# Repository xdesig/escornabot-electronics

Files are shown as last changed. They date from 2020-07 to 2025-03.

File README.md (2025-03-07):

# escornabot
Educational robot
scornabot is an open source/hardware project that aims to bring robotics and programming to children.

The basic Escornabot can be programmed with the robot's buttons to execute sequence of movements. From this, imagination is the only one limit to the possibilities.

- Hey! That you are describing looks very much like a Bee-Bot!

- Yes, but much better for several reasons. Among them, I will highlight a few:

It is made by you. And your pupils, children, young cousins... Everyone can help by participating in the process from the beginning. The pleasure of building your own escornabot converts the experience in something great, specially when children are involved in it.

It is a open hardware (OSHW) and free software (FOSS) so you can adapt its characteristics to your needs: to put sensors, LEDs, change the aperture angle of rotation, the distance it moves at each step... whatever that comes to mind.

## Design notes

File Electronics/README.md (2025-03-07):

## Catalog
- [Escorna CPU][CPU01] is 50x50mm to 50x100mm board to use with Arduino Nano. It integrates keypad on board on 2x

- [Escorna_CPU_2_4][CPU240] It is a pcb that integrates an ATmega328P, a step-up (to use 1.2V batteries) and the rest of the electronics needed to build an Escornabot.

- [Arduino Shield][ARD01] is an Arduino Uno compatible
  shield ready to use with the Escornabot's motors and also integrates a keypad.

- [Cervus][CER01] is a board based on powerful ATmega32u4
  microcontroler and compatible with Arduino shields.
- [E_Keypad][KEY01] Is a 50x50mm board with 6  and 5 buttons and
  connects to any Escornabot.

- [E_KEY_BT][E_KEY_BT] Escornabot keyboard with MakeyMakey type sensors on the E_KEY_BT board.
   Any object that is minimally conductive can be used. Adjusting the value
   threshold: higher for less sensitivity, nothing needs to be changed in the
   robot firmware.

- [E_KEY_FICHA][E_KEY_FICHA] It allows the programming of Escornabot using printed or cut-out cards (cardboard ..) communicating the commands via Bluetooth.
  using @arduino Nano, easy to print, manageable and expandable to 15 "Tabs" thanks to the firmware of @caligari_pub

- [escoRnaFID][RnaFID]PCB for the project for children with visual impairment or blindness,
  developed by Angel Villanueva [@avilmaru][@avil] to control an Escornabot with RFID cards

## License

Every content in this repo, otherwise specified under subdirectories, is
licensed under [Creative Commons BY-SA][LICENSEcc] or [CERN Open Hardware Licence -W- V2][OHL-W-V2].
(by [XDeSIG][XDE01])

## To buy boards

Developer don't produce boards to sell. Under [_provider_][provider]
directory there are instructions to order yourself.

Are you a board provider? Please, send us your buyer's guide! :-)

[CPU01]: EscornaCPU
[CPU240]: https://github.com/xdesig/escornabot-electronics/tree/master/Electronics/EscornaCPU/2.x/2.40
[ARD01]: ArduinoShield
[CER01]: Cervus
[KEY01]: E_KEYPAD
[RnaFID]: escoRnaFID
[E_KEY_BT]: E_KEY_BT
[@avil]: https://twitter.com/avilmaru
[XDE01]: https://twitter.com/xdesig
[provider]: https://www.pcbway.com/project/member/?bmbno=6FE4DE76-9D11-4C
[LICENSEcc]: https://creativecommons.org/licenses/by-sa/3.0/es
[OHL-W-V2]: https://ohwr.org/project/cernohl/wikis/Documents/CERN-OHL-version-2

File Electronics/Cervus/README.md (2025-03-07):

# Cervus 2.001

## Catalog

- [Cervus][KEY01] (by [Xdesig][XDE01]) is a 50x50mm board, it controls any Escornabot, and is an atmega development PCB (Arduino Leonardo compatible)

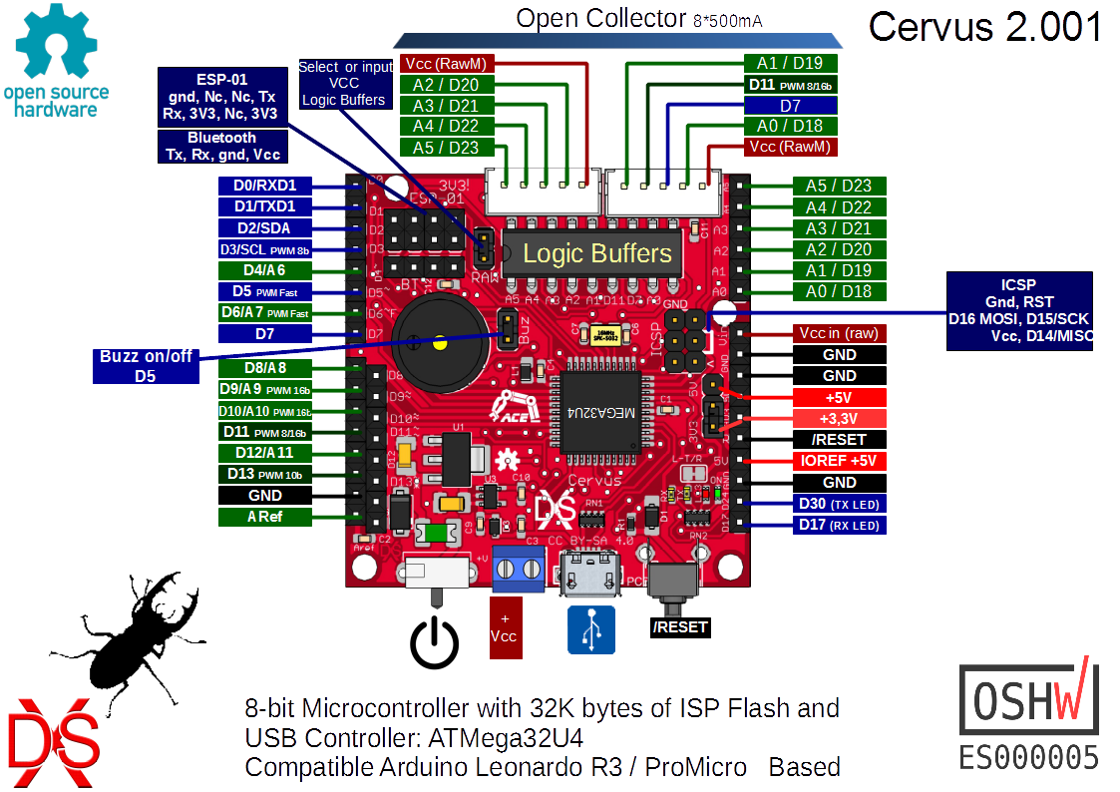
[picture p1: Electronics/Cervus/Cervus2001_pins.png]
Top view


## License

Every content in this repo, otherwise specified under subdirectories, is
licensed under [Creative Commons BY-SA](LICENSE).

## To buy boards

Developers don't produce boards to sell. Under [PCBWAY]

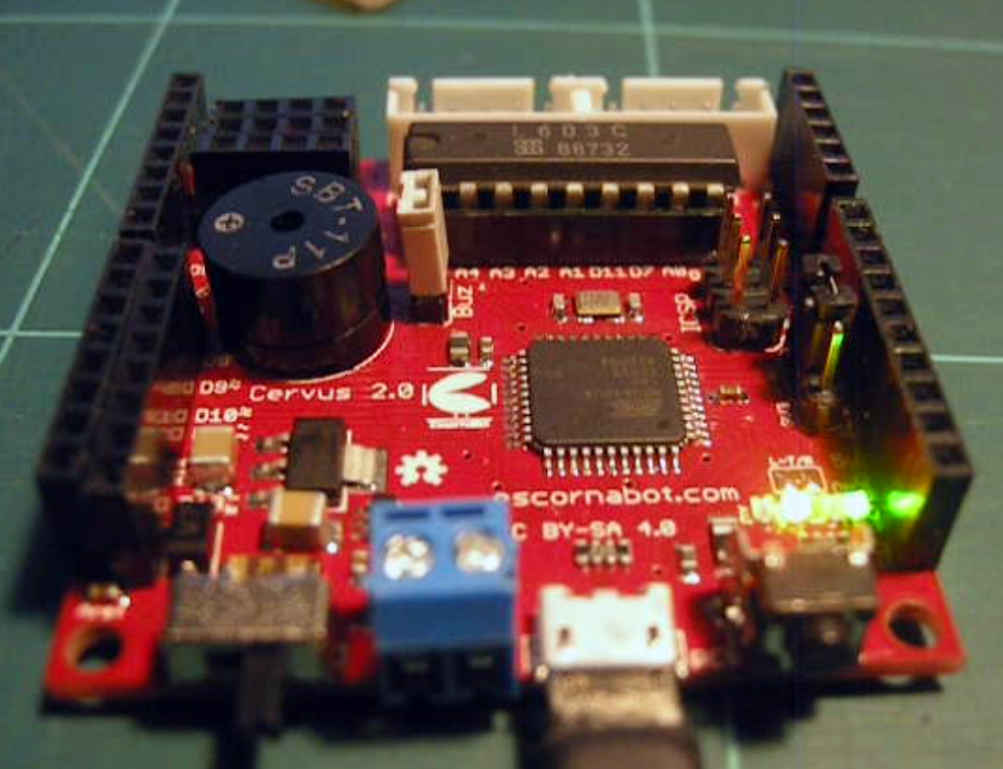
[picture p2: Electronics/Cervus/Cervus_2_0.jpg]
Bottom view


[KEY01]: Keypad
[PCBWAY]: https://www.pcbway.com/project/shareproject/Cervus_Arduino_Leonardo_Coompatible.html
[XDE01]: https://twitter.com/xdesig

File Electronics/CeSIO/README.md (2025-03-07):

# CeSIO Cervus Shield I/O  V 000

A pcb with all the I / O of Cervus (compatible with Arduino PCBs), available in connectors accompanied by + V and Gnd, whereby groups we can choose how we feed it: a + 5V, A + 3.3V or external V, giving the possibility to connect elements such as sensors, servos and other devices, has connector for ESP01 and Bluetooth.

It allows to use the DD05CVSA module to control a Li-ion battery.

Buy PCB in [PCBWAY]

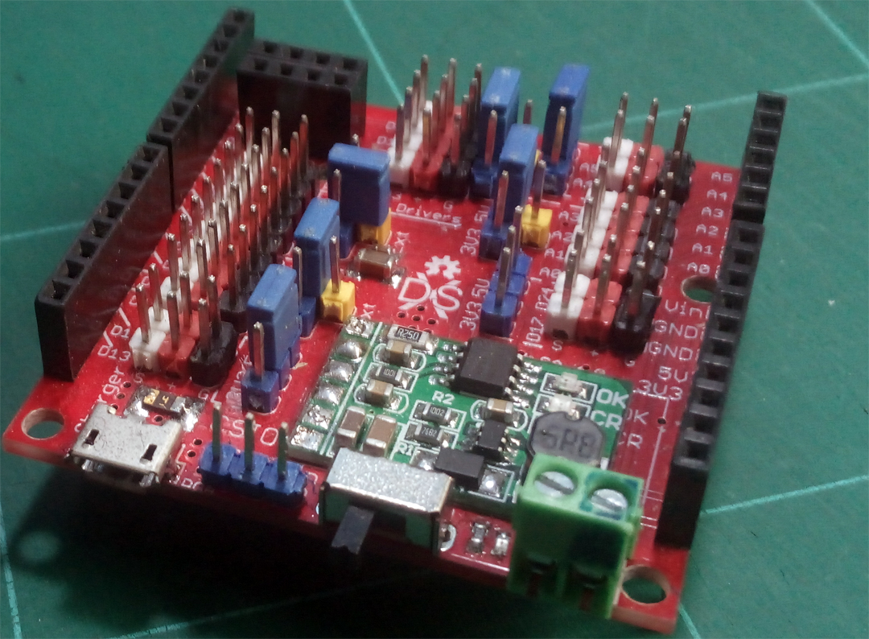
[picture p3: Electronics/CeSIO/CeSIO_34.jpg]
Top view

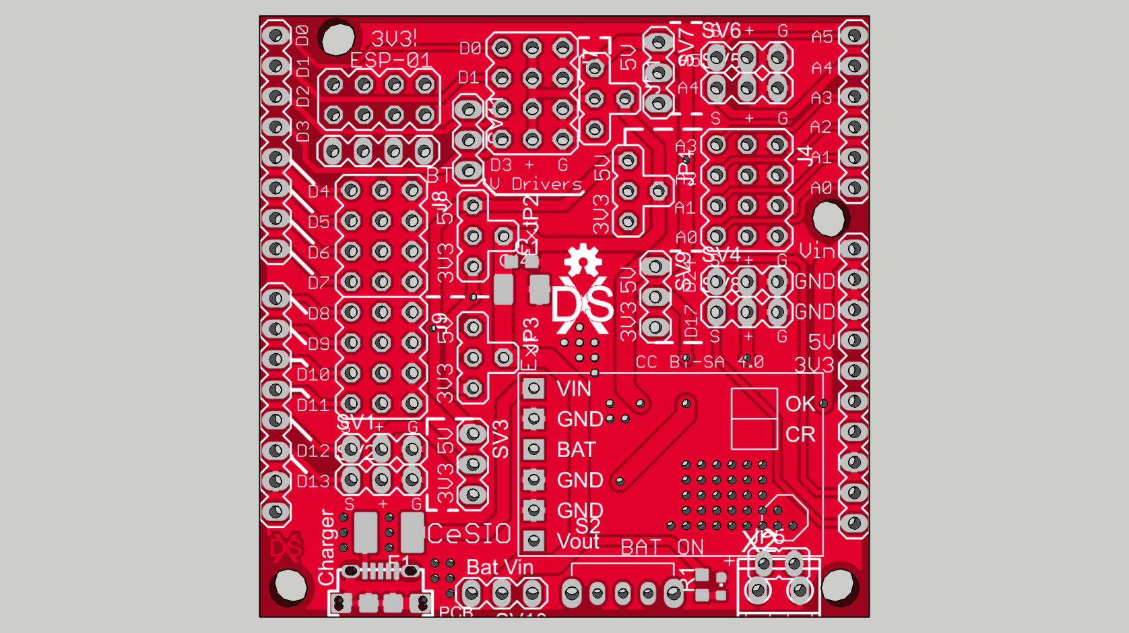
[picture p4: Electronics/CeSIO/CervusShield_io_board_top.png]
Render

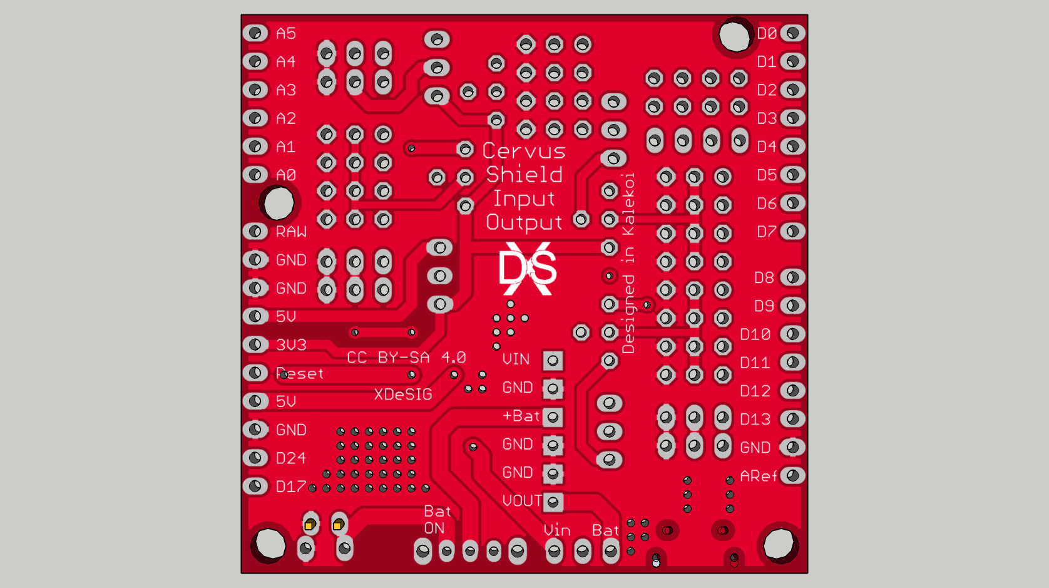
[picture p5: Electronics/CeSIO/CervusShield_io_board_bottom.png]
Real


## Author and license
* Author: [XDeSIG][TWI01]
* License: [Attribution-ShareAlike 4.0 International] [CCBY-SA4.0]

<!-- links -->

[CCBY-SA4.0]: http://creativecommons.org/licenses/by-sa/4.0/
[TWI01]: https://twitter.com/xdesig
[PHT]: CeSIO_34.jpg
[RENDER]: CervusShield_io_board_top.png
[Real]: CervusShield_io_board_bottom.png
[PCBWAY]: https://www.pcbway.com/project/shareproject/CeSIO_Cervus_Shield_I_O.html

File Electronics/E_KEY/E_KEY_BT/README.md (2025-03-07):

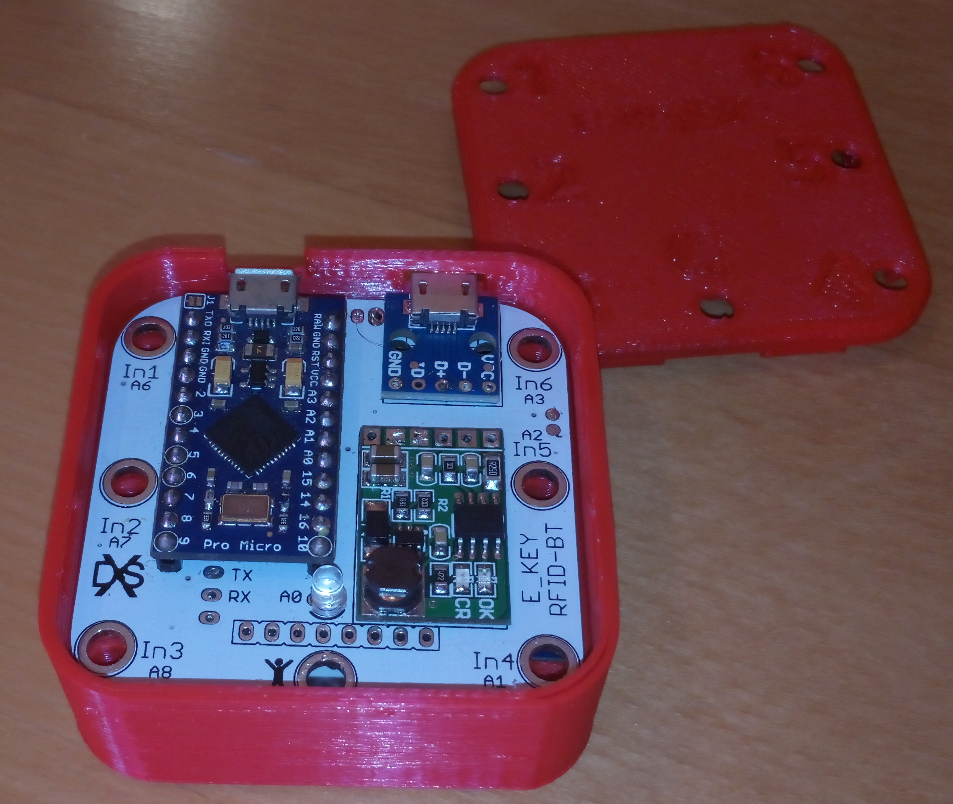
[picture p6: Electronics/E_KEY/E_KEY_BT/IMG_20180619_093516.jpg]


## E_KEY_BT
Escornabot keyboard with MakeyMakey type sensors.
   Any object that is minimally conductive can be used. Adjusting the value
   threshold: higher for less sensitivity, nothing needs to be changed in the
   robot firmware.
   
## License

Every content in this repo, otherwise specified under subdirectories, is
licensed under [Creative Commons BY-SA][LICENSEcc] or [CERN Open Hardware Licence -W- V2][OHL-W-V2].
(by [XDeSIG][XDE01])

## To buy boards

Developer don't produce boards to sell. Under [_provider_][provider]
directory there are instructions to order yourself.

Are you a board provider? Please, send us your buyer's guide! :-)

[imax]: https://github.com/xdesig/escornabot-electronics/blob/master/Electronics/E_KEY_BT/IMG_20180619_093516.jpg

[XDE01]: https://twitter.com/xdesig
[provider]: https://www.pcbway.com/project/member/?bmbno=6FE4DE76-9D11-4C
[LICENSEcc]: https://creativecommons.org/licenses/by-sa/3.0/es
[OHL-W-V2]: https://ohwr.org/project/cernohl/wikis/Documents/CERN-OHL-version-2

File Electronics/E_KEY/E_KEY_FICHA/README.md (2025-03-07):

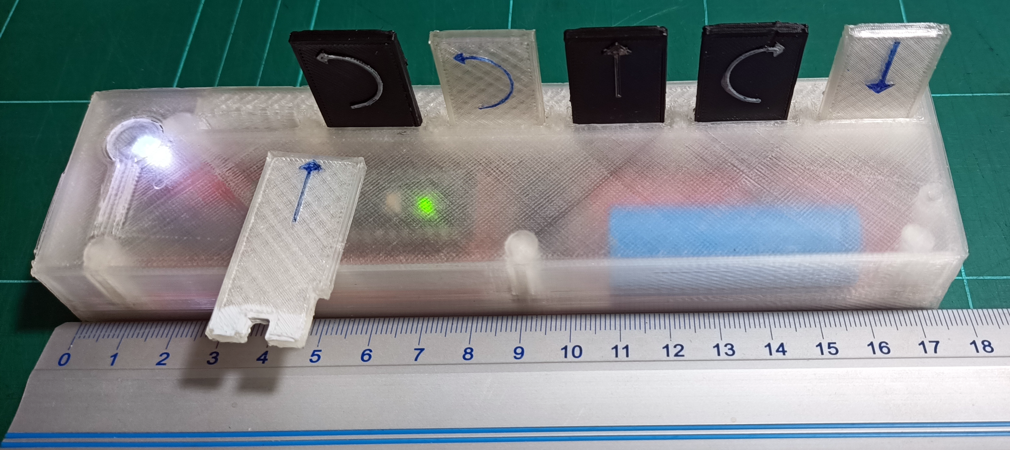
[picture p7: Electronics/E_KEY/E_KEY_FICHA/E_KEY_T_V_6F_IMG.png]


## EscornabotFicha   
                     certification.oshwa.org/list.html
## E_KEY_FICHA (Tag)
It allows the programming of Escornabot using printed or cut-out cards (cardboard ..) communicating the commands via Bluetooth 
using @arduino Nano, easy to print, manageable and expandable to 15 "Tabs" thanks to the firmware of @caligari_pub.

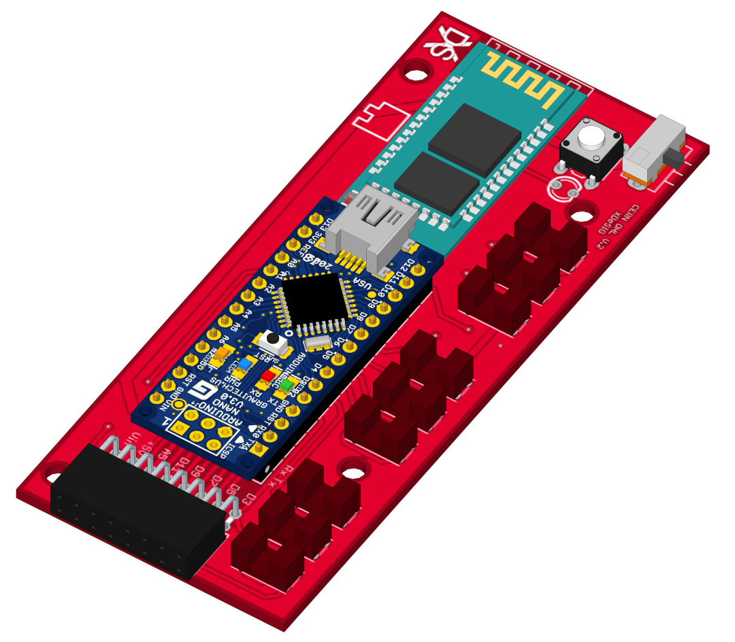
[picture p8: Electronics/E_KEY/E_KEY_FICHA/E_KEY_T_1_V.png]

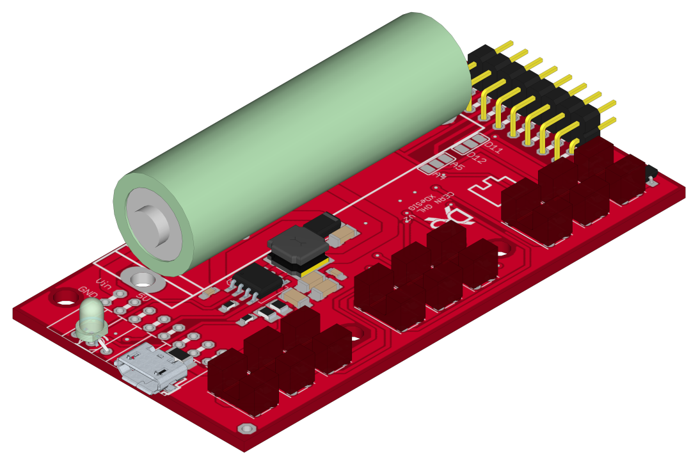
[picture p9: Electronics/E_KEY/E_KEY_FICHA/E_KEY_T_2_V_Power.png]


## Number of Tags (Fichas)
To use six tags we need the PCBs E_KEY_T_1_V and E_KEY_T_2_V the latter with the power components.

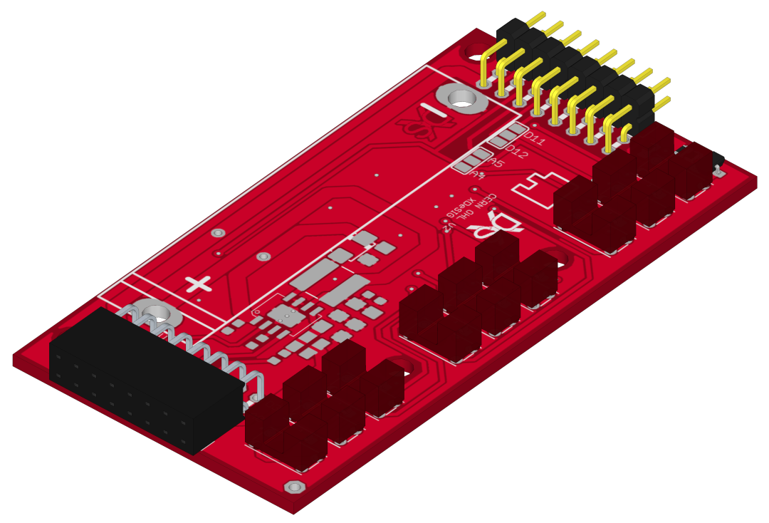
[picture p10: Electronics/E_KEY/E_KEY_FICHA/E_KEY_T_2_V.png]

 If we want to have more chips (9 to 15) we will put intermediate circuits E_KEY_T_2_V without the power supply electronics.

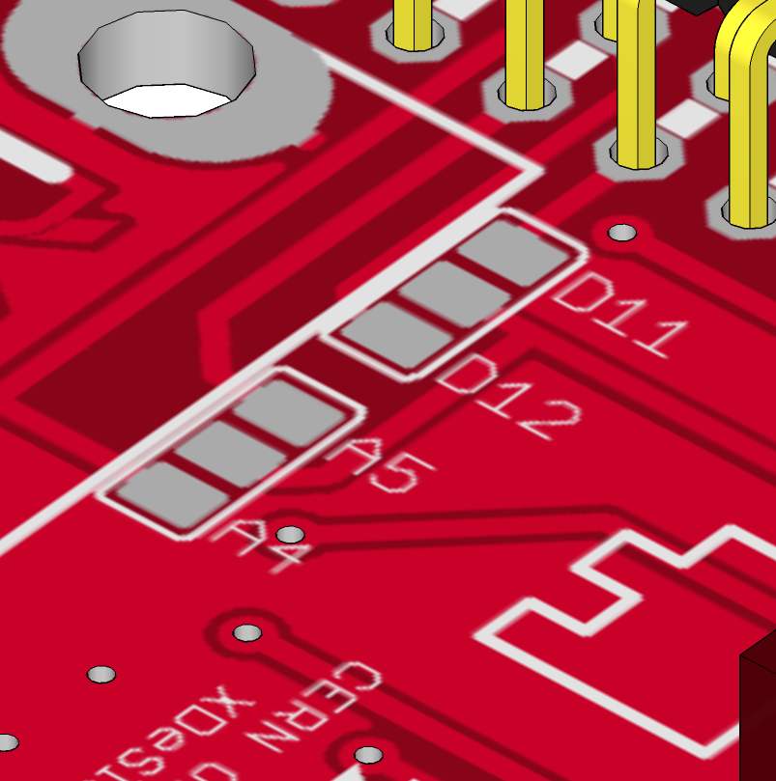
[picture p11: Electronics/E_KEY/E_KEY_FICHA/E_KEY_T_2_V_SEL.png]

The selection will always be configured on the end plates, according to the firmware "configuration.h".
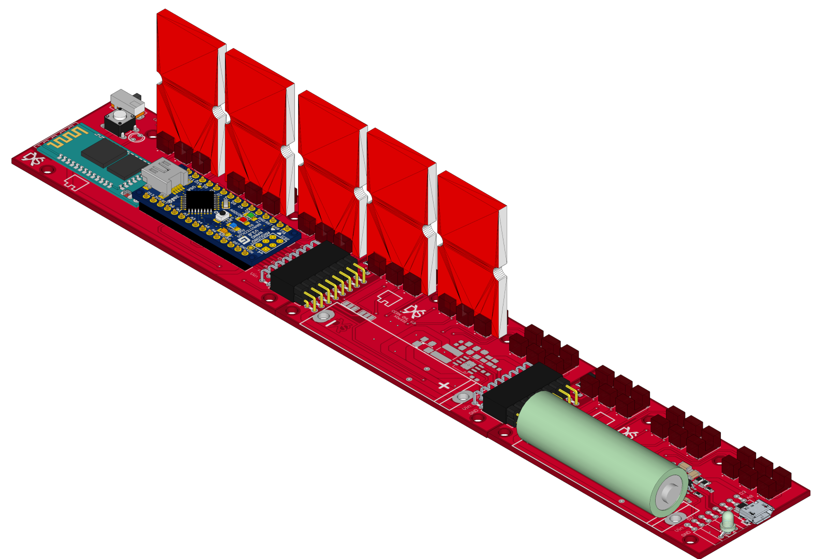
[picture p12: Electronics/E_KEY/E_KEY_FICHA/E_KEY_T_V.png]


## License hardware and docu.

Every content in this repo, otherwise specified under subdirectories, is
licensed under [Creative Commons BY-SA][LICENSEcc] or [CERN Open Hardware Licence -W- V2][OHL-W-V2].
(by [XDeSIG][XDE01])

## License software.
  Copyright (C) 2020  Rafa Couto <caligari@treboada.net>
    This program is free software: you can redistribute it and/or modify
    it under the terms of the GNU General Public License as published by
    the Free Software Foundation, either version 3 of the License, or
    (at your option) any later version.
    This program is distributed in the hope that it will be useful,
    but WITHOUT ANY WARRANTY; without even the implied warranty of
    MERCHANTABILITY or FITNESS FOR A PARTICULAR PURPOSE.  See the
    GNU General Public License for more details.
    You should have received a copy of the GNU General Public License
    along with this program.  If not, see <https://www.gnu.org/licenses/>.

## Certification OSHWA [ES000024][OSHWAes000024]

## To buy boards

Developer don't produce boards to sell. Under [_provider_][provider]
directory there are instructions to order yourself.

Are you a board provider? Please, send us your buyer's guide! :-)

[imax]: https://github.com/xdesig/escornabot-electronics/blob/master/Electronics/E_KEY_BT/IMG_20180619_093516.jpg

[XDE01]: https://twitter.com/xdesig
[provider]:  http://
[LICENSEcc]: https://creativecommons.org/licenses/by-sa/3.0/es
[OHL-W-V2]: https://ohwr.org/project/cernohl/wikis/Documents/CERN-OHL-version-2
[OSHWAes000024]: https://certification.oshwa.org/es000024.html

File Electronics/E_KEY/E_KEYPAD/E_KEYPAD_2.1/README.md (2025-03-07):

# E_keyPad 2.10

## Catalog

- [Keypad][KEY01] (by [Xdesig][XDE01]) is a 50x50mm board with 5 buttons and
  connects to any Escornabot.

## License

Every content in this repo, otherwise specified under subdirectories, is
licensed under [Creative Commons BY-SA](LICENSE).

## To buy boards

Developers don't produce boards to sell. Under [PCBWAY]

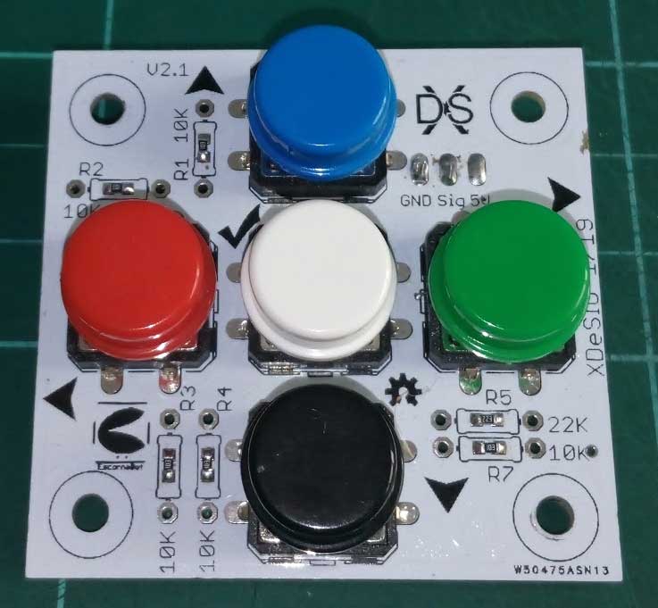
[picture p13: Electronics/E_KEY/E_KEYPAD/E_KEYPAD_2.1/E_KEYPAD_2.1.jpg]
Bottom view


[KEY01]: Keypad
[PCBWAY]: https://www.pcbway.com/project/shareproject/W50475ASN5_Escorna_bot_2_1_Gerber.html
[XDE01]: https://twitter.com/xdesig

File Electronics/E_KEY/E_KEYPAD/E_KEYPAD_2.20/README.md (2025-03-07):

# E_keyPad 2.20

## Catalog

- [Keypad][KEY01] (by [Xdesig][XDE01]) is a 50x50mm board with 5 buttons, 4 LEDs and
  connects to any Escornabot.

## License

Every content in this repo, otherwise specified under subdirectories, is
licensed under [Creative Commons BY-SA](LICENSE).
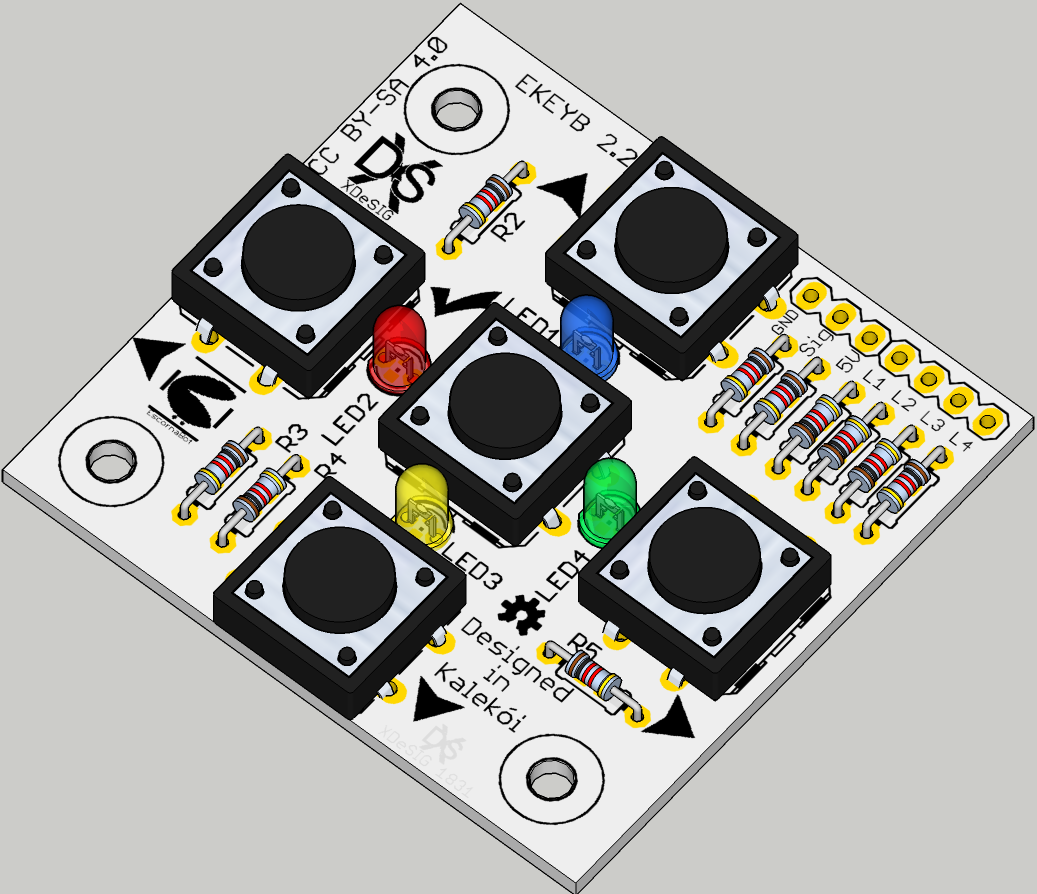
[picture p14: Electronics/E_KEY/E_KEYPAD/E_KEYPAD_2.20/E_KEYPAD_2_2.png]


## To buy boards

Developers don't produce boards to sell. Under [PCBWAY]

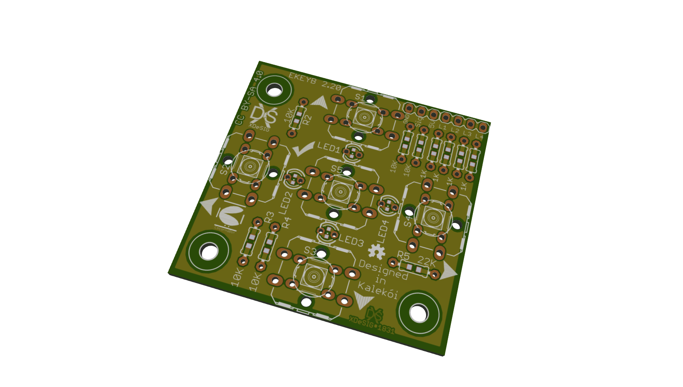
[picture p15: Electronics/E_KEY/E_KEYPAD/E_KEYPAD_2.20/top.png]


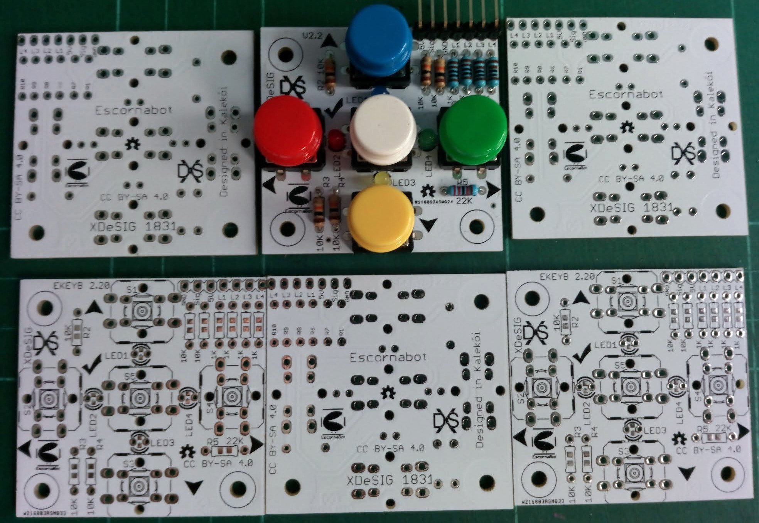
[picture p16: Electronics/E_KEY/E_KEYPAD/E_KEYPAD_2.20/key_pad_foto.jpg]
Bottom view


[KEY01]: Keypad
[PCBWAY]: https://www.pcbway.com/project/shareproject/E_KEYPAD_2_2.html
[XDE01]: https://twitter.com/xdesig

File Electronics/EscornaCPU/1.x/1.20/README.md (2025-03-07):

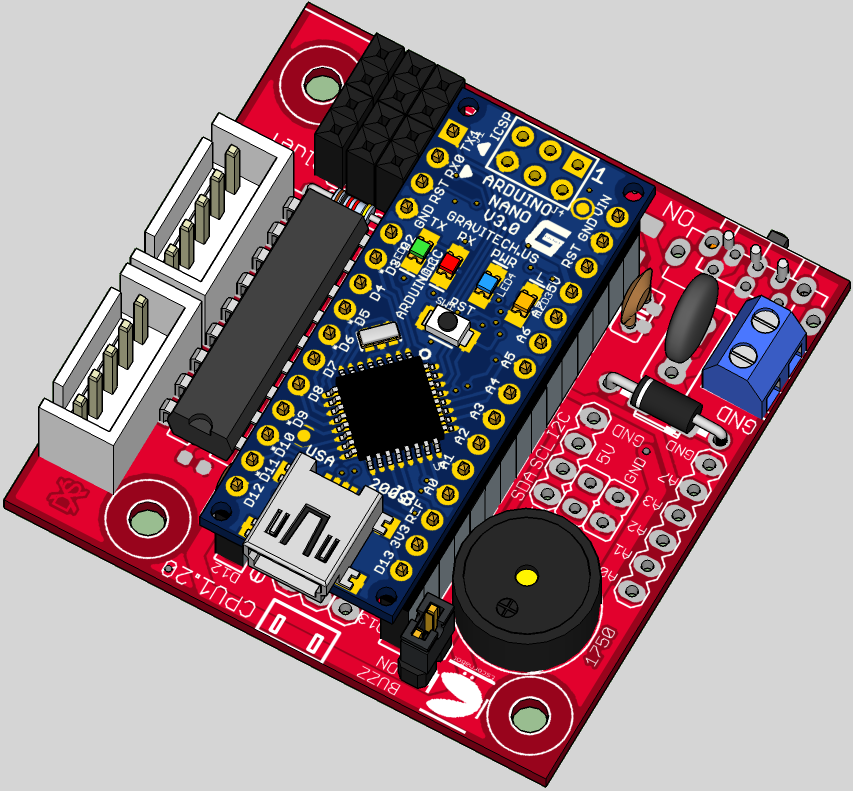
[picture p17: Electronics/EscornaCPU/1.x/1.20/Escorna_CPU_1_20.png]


## Escorna CPU 1.20

It allows to include an Arduino Uno for the control of the robot, an ESP-01 or Bluetooth (for communications).
You can connect them to different keypads to manage the robot, I recommend the [E_KEYPAD_2.20]

## License

Every content in this repo, otherwise specified under subdirectories, is
licensed under [CERN Open Hardware Licence -W- V2][OHL-W-V2].
(by [XDeSIG][XDE01])

## To buy boards

Developer doesn't produce boards to get money. [provider]

Are you a board provider? Please, send us your buyer's guide! xdesig@gmail.com

[XDE01]: https://twitter.com/xdesig
[provider]: https://www.pcbway.com/project/shareproject/W50475ASN23_Escorna_CPU_1_20.html
[LICENSEcc]: https://creativecommons.org/licenses/by-sa/3.0/es
[OHL-W-V2]: https://ohwr.org/project/cernohl/wikis/Documents/CERN-OHL-version-2
[E_KEYPAD_2.20]: https://github.com/xdesig/escornabot-electronics/tree/master/Electronics/E_KEYPAD/E_KEYPAD_2.20

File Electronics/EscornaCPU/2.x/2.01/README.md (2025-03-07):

# Escorna CPU + Keypad /  (version 2.10)

## Changes 2.10

  - Keyboard pin is A7 instead A4 so I2C interface is free to use in your projects.
  - Polarity inversion protection by diode anti-parallel and resetable fuse.
  - Power switch was moved to better position on the board 'backside'.
  - Switch compatibility with SK-12D07 and SK-12F14.
  - Keypad can use tactile switches 6mm, 12mm and 12mm with LED. See more below.
  - One of the EscornaShield connector was removed (obsolete).
  - Continuing the connector D13 - RAW (expand connections)
  - Buzzer, power connectors and drivers can be connected on both sides of the board.
  - Holes for holders continue in the same position (PCB extended 5.1mm backwards).
  - Full compatible one side, with an operative Escornabot (excepting the expansion connector).

## Tactile switches with LED

LED assignments:    --        [suggested color][wiki]

| KEY / signal| Color |
|---|---|
| UP  / A0 | Blue  |
| RIGHT / A3  | Gren  |
| DOWN / A2 | Yelow |
| LEFT / A1 | Reed  |
| GO / D13 | WiteA |

The LEDs can be disabled by cutting a small wire-jumper, you can use these outputs for other things. Reconnect with a small welding.

## Expansion connector

2.54mm double strip

| row 1 | row 2 |
|---|---|
| 3V3 | 3V3 |
| 5V | 5V |
| D13 / SCK | A0 / D14 |
| A1  / D15 | A2 / D16 |
| A3  / D17 | A4 / D18 / SDA |
| A5  / D19 / SCL | A6 / No Pullup |
| GND | GND |
|-----------------|----------------|

## Author and license

* Author: [XDeSIG][TWI01]
* License: [Creative Commons BY-SA][CCBYSA]

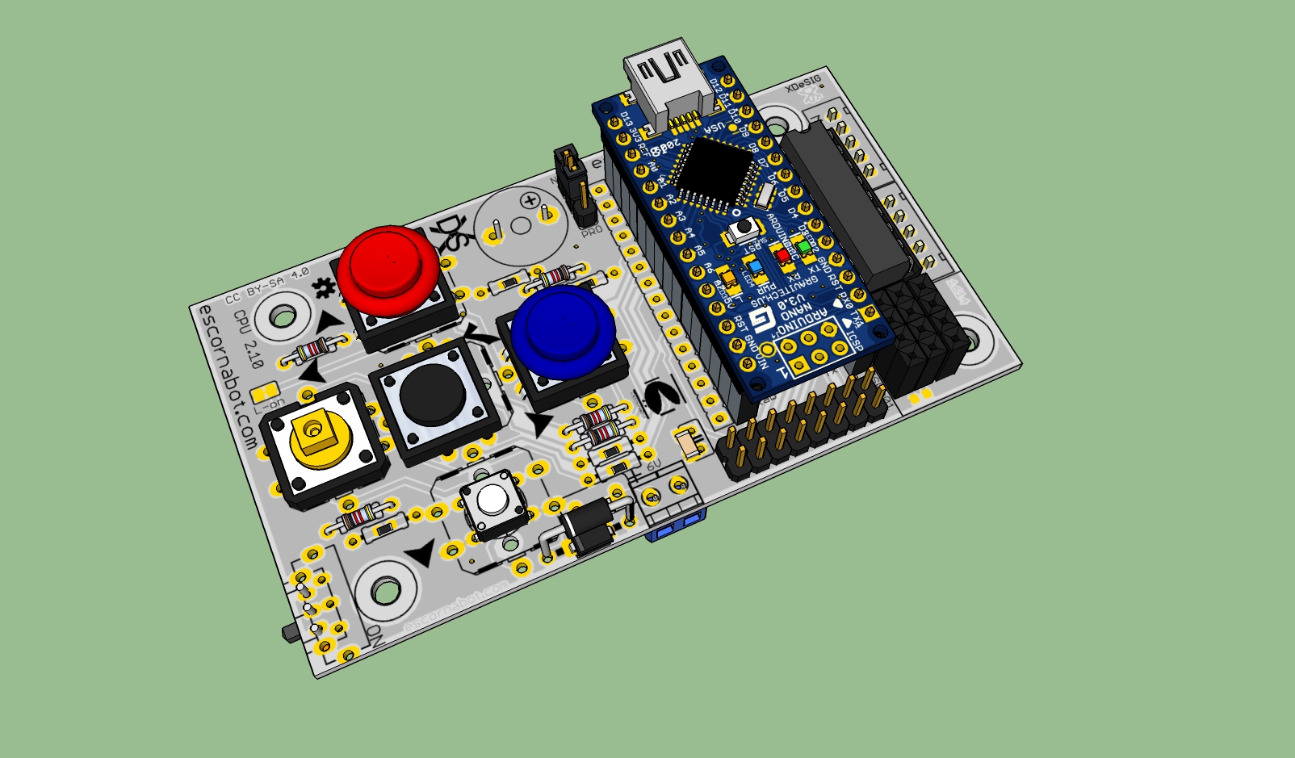
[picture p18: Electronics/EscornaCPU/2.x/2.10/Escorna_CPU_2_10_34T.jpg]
Render Escorna CPU 2.10


<!-- links -->
[wiki]: https://en.wikipedia.org/wiki/Navigation_light
[CCBYSA]: http://creativecommons.org/licenses/by-sa/4.0/
[TWI01]: https://twitter.com/xdesig
[RENDER]: Escorna_CPU_2_10_34T.jpg

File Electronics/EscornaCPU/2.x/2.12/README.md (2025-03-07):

# EscornaCPU 2.12 by [XDesig][XDE01]

- Control of Escornabot through keyboard, Bluetooth HC-05, 06 and WiFi ESP-01.
- Central connector, for screen oled or I2C device.
- All components screen printed with your value.
- SMD (Surface Mount Device). or THT (through hole). Except the 3.3V and C1.2 regulator, 
- More info - [Caracteristicas\_CPU2\_12.pdf (in Galician)][NOT01]

- [Escorna\_CPU\_2\_12\_Gerber.zip (Gerber files)][GER01]
- [Escorna\_CPU\_2\_12.brd (Eagle Board)][BOA01]
- [Escorna\_CPU\_2\_12.sch (Eagle Schematics)][SCH01]
- [Escorna\_CPU\_2\_12\_ESQ.pdf (PDF Schematichs)][SCH02]
- [Escorna\_CPU\_2\_12\_measures.pdf (Board measures)][MEA01]

## License

Every content in this repo, otherwise specified under subdirectories, is
licensed under [Creative Commons BY-SA](LICENSE).

## To buy boards

Developer don't produce boards to sell. Under [PCBWAY]

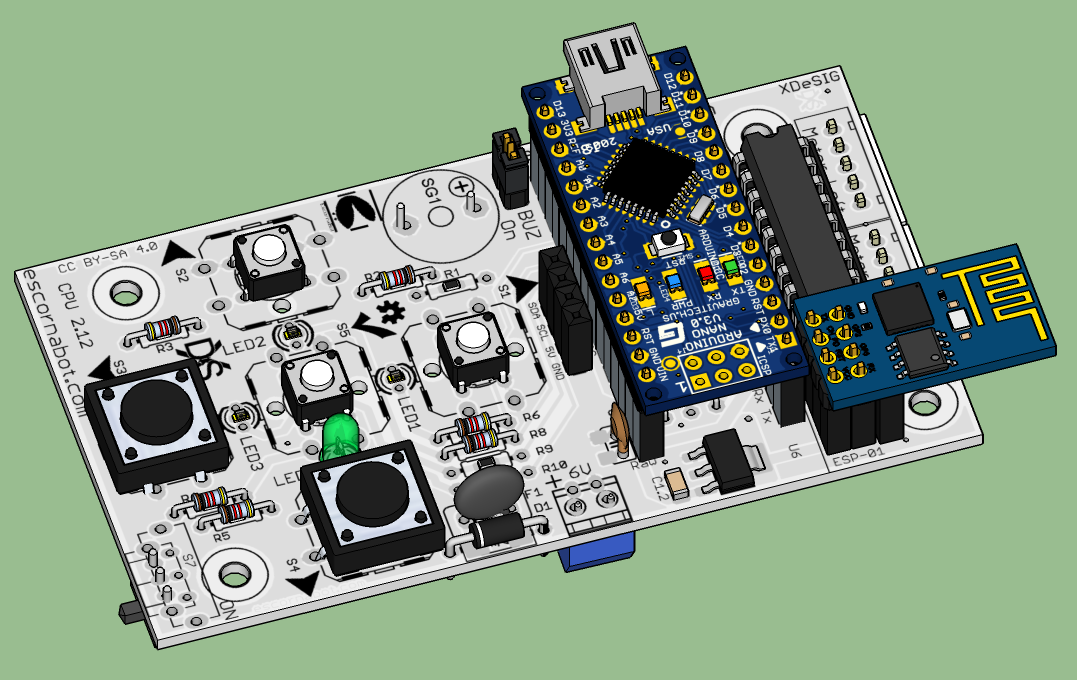
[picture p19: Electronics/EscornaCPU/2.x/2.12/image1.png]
Top view

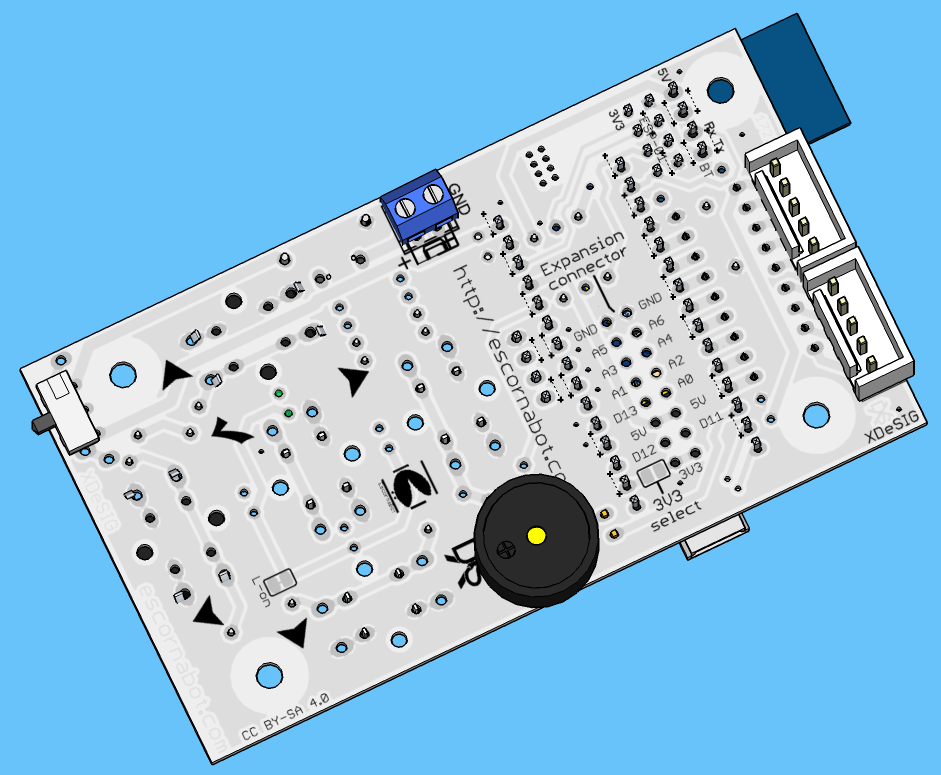
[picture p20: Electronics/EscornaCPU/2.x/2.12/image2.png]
Bottom view


[GER01]: Escorna_CPU_2_12_Gerber.zip
[BOA01]: Escorna_CPU_2_12.brd
[SCH01]: Escorna_CPU_2_12.sch
[SCH02]: Escorna_CPU_2_12_ESQ.pdf
[MEA01]: Escorna_CPU_2_12_measures.pdf
[NOT01]: Caracteristicas_CPU2_12.pdf
[PCBWAY]: https://www.pcbway.com/project/shareproject/W50475ASN19_Escorna_CPU_2_12_Gerber.html
[XDE01]: https://twitter.com/xdesig

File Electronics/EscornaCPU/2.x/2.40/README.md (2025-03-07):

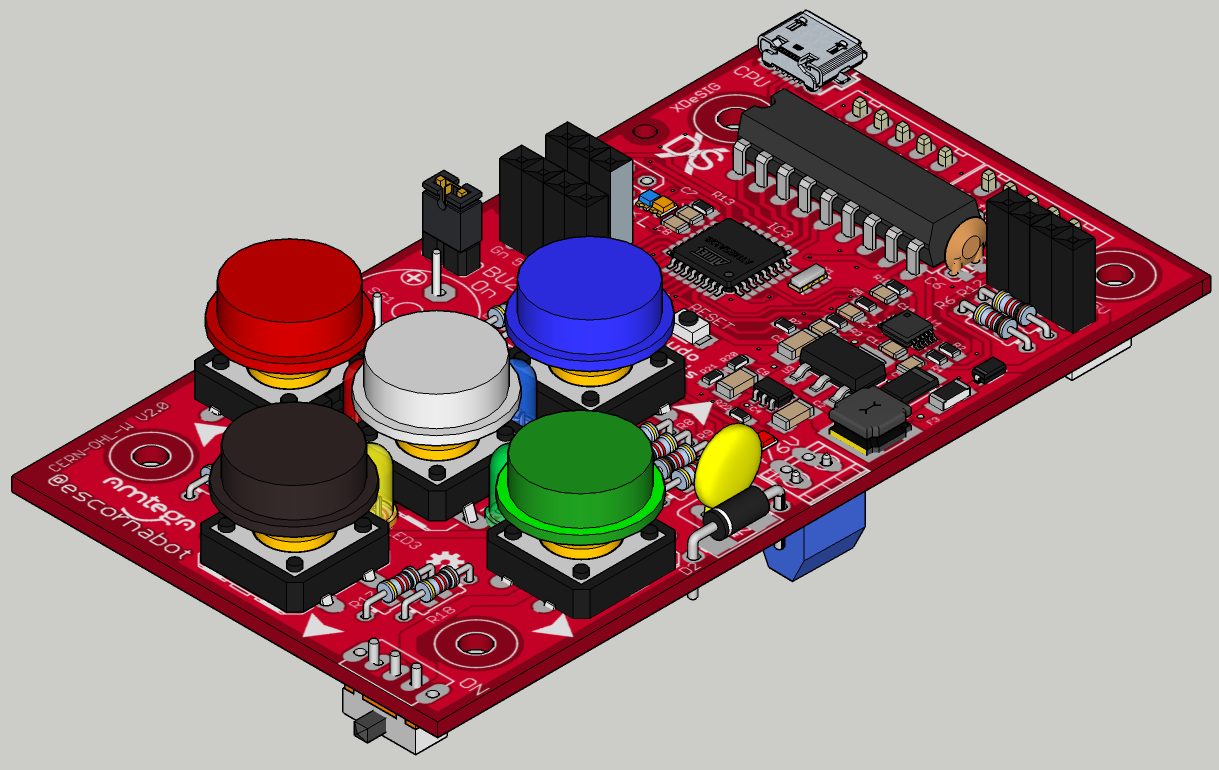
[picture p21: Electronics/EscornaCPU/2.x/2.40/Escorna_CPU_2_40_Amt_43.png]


## Escorna CPU 2.4
This PCB integrates an ATmega328P, a step-up (great to use with 1.2V batteries, suggestion made by [caligari](https://github.com/rafacouto)) and the rest of the electronics needed to build a full-compatible Escornabot.
USB communications are supported by CH340E<br>
Arduino Uno, Arduino Nano compatible or ATmega minicore

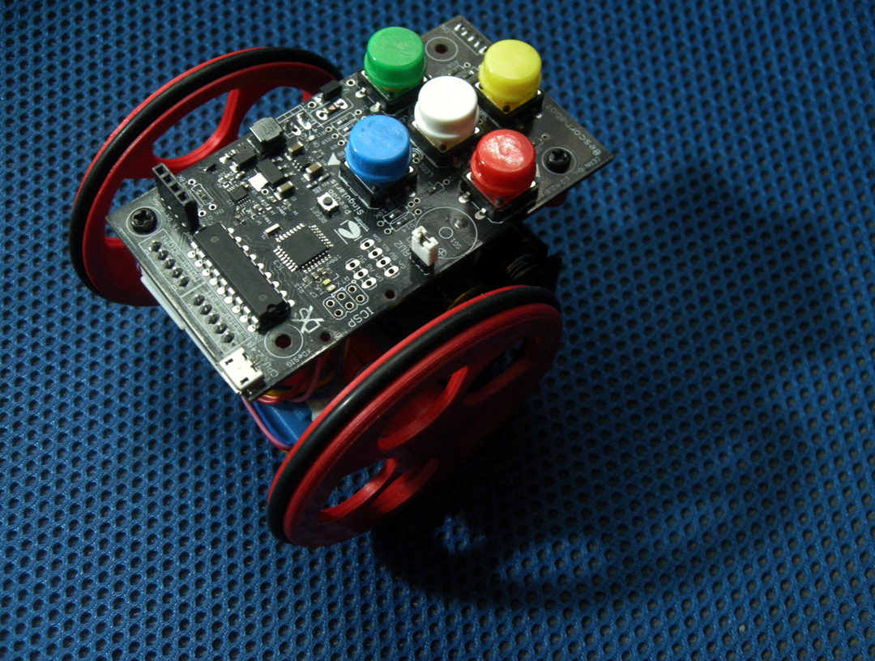
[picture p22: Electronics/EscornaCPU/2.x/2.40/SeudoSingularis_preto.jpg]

   
## License



<br><br><br><br>

## Open Hardware Certification program



<br><br><br><br><br><br><br>

## To buy boards
Developer doesn't produce boards to get money. [_provider_][provider]

Are you a board provider? Please, send us your buyer's guide! xdesig@gmail.com

[XDE01]: https://twitter.com/xdesig
[provider]: https://www.pcbway.com/project/shareproject/Escorna_CPU_2_4.html
[LICENSEcc]: https://creativecommons.org/licenses/by-sa/3.0/es
[OHL-W-V2]: https://ohwr.org/project/cernohl/wikis/Documents/CERN-OHL-version-2

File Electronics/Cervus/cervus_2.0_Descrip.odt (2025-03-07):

Zocalo ( tiras de pins esquerdo) 8 + 8 pins: Zocalo ( tiras de pins dereito) 6 +9 pins

Pin Atmega Leonardo Pin Atmega Leonardo

1 PD2 D0/RX 1 PF0 A5

2 PD3 D1/TX 2 PF1 A4

3 PD1 D2/SDA 3 PF4 A3

4 PD0 D3/SCL~ 4 PF5 A2

5 PD4 D4/A6~ 5 PF6 A1

6 PC6 D5 ~~ 16bits 6 PF7 A0

7 PD7 D6/A7 ~HSpeed

8 PE6 D7

8 RAW Vin

9 PB4 D8/A8 9 GND GND

10 PB5 IO9/A9 ~~ 16bits 10 GND GND

11 PB6 IO10/A10 ~~ 16bits 11 +5V +5V

12 PB7 IO11 ~~ 8/16Bits 12 +3V3 3.3V

13 PD6 IO12/A11~HSpeed 13 RESET RESET

14 PC7 IO13 ~10bits 14 +5V +5V

15 GND GND 15 D24/LTX N/C

16 Aref Aref 16 D17/LRX ( )

En grosa as conexións utilizadas por Escornabot.

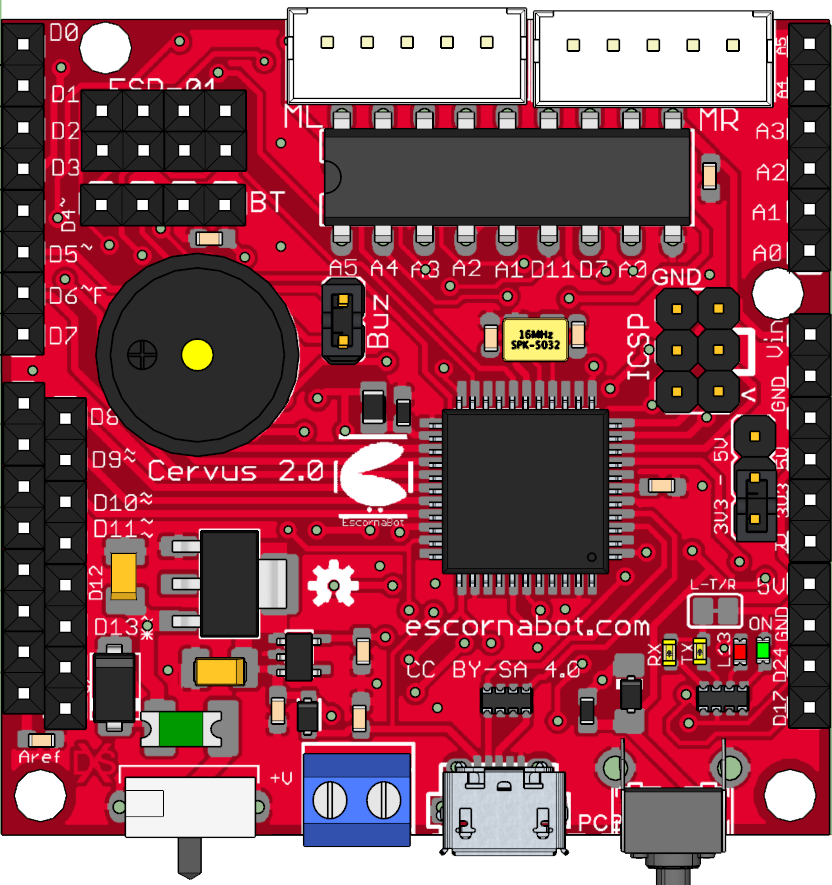
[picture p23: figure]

Selección de Alimentación 3,3V e 5V

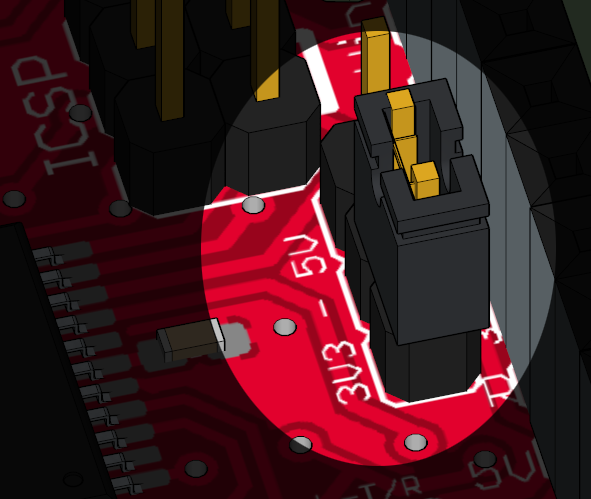
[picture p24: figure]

Posibilidade de descontar os leds ( LRX. LTX ) da placa para que non utilicen corrente das saídas ( D24, D17 ).


Igualmente co led L13 conectado a D13


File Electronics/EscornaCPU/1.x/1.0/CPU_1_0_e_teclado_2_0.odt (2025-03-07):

Esquema - Escorna CPU 1.0 - Atallo os ficheiros: http://goo.gl/NUfwrV


JP1 Interruptor alimentación

JP2 podemos elixir onde conectar o Zoador,

Opcións: Sen ponte Modo silencioso (adestrar sen molestar os que durman ou estudan)

Ponte 1 – 2 Placas Pro-mini e Pro-micro

X3 conector teclado externo compatible ca versión 1 e 2, non é preciso cando se conecta o teclado Shield.

SV4 conector para modulo Bluetooth (ou outro que precise Tx e Rx)

Montaxe

Placa - Escorna CPU 1.0 -


Nota: Se se soldan os condensadores Cx non soldar os condensadores Cx.1

Dimensións Placa - Escorna CPU 1.0 -


O pad que se atopa (Baixo dereita) o lado de Tx de SV4 pode tradearse a 3mm para ter outro punto de amarre

Esquema - Escorna Shield botoneira 2.0B - Atallo os ficheiros: http://goo.gl/bZ2Vkc


Cando non utilizamos o teclado en modo shield podemos conectalo a placa CPU mediante J2. (ollo xa non teremos acceso o resto dos conectores led...)

SJ1 é un selector por soldadura para elixir a alimentación do conector J1

Opcións : 1 - 2 a tensión no pin 5 é a de entrada (RAW).

2 - 3 a tensión no pin 5 é a regulada polo arduino (5Vcc)

Montada independente Montada como Shield


Escorna CPU 1.0 e Botoneira 2.0 (shield) + Ideas

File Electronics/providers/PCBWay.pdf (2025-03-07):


Pedir placas para escornabot a https://www.pcbway.com

Elixe a placa

Escorna_CPU_2_12 (https://www.pcbway.com/project/shareproject/W50475ASN19_Escorna_CPU_2_12_Gerber.html)

Botoneira 2_1 (https://www.pcbway.com/project/shareproject/W50475ASN5_Escorna_bot_2_1_Gerber.html)

Escorna_CPU_1_20 (https://www.pcbway.com/project/shareproject/W50475ASN23_Escorna_CPU_1_20.html)


Pedir placas para escornabot a https://www.pcbway.com

Selecciona 10 placas, custan o mesmo que 5 :-)

Agora toca esperar, ata que comproben que se pode facer, unha hora ou +

Elixe a forma de envío (ollo con DHL... cobran aduanas e IVA) eu uso: E-packet

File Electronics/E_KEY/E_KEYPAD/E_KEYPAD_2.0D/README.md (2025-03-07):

# EscornaShield Keypad (version 2)

* Author: [XDeSIG][TWI01]
* License: [Creative Commons BY-SA][CCBYSA]

Render EscornaShield Keypad

[CCBYSA]: http://creativecommons.org/licenses/by-sa/4.0/
[TWI01]: https://twitter.com/xdesig
[RENDER]: Escorna_Shield_botoneira_2_0D_mont.jpg

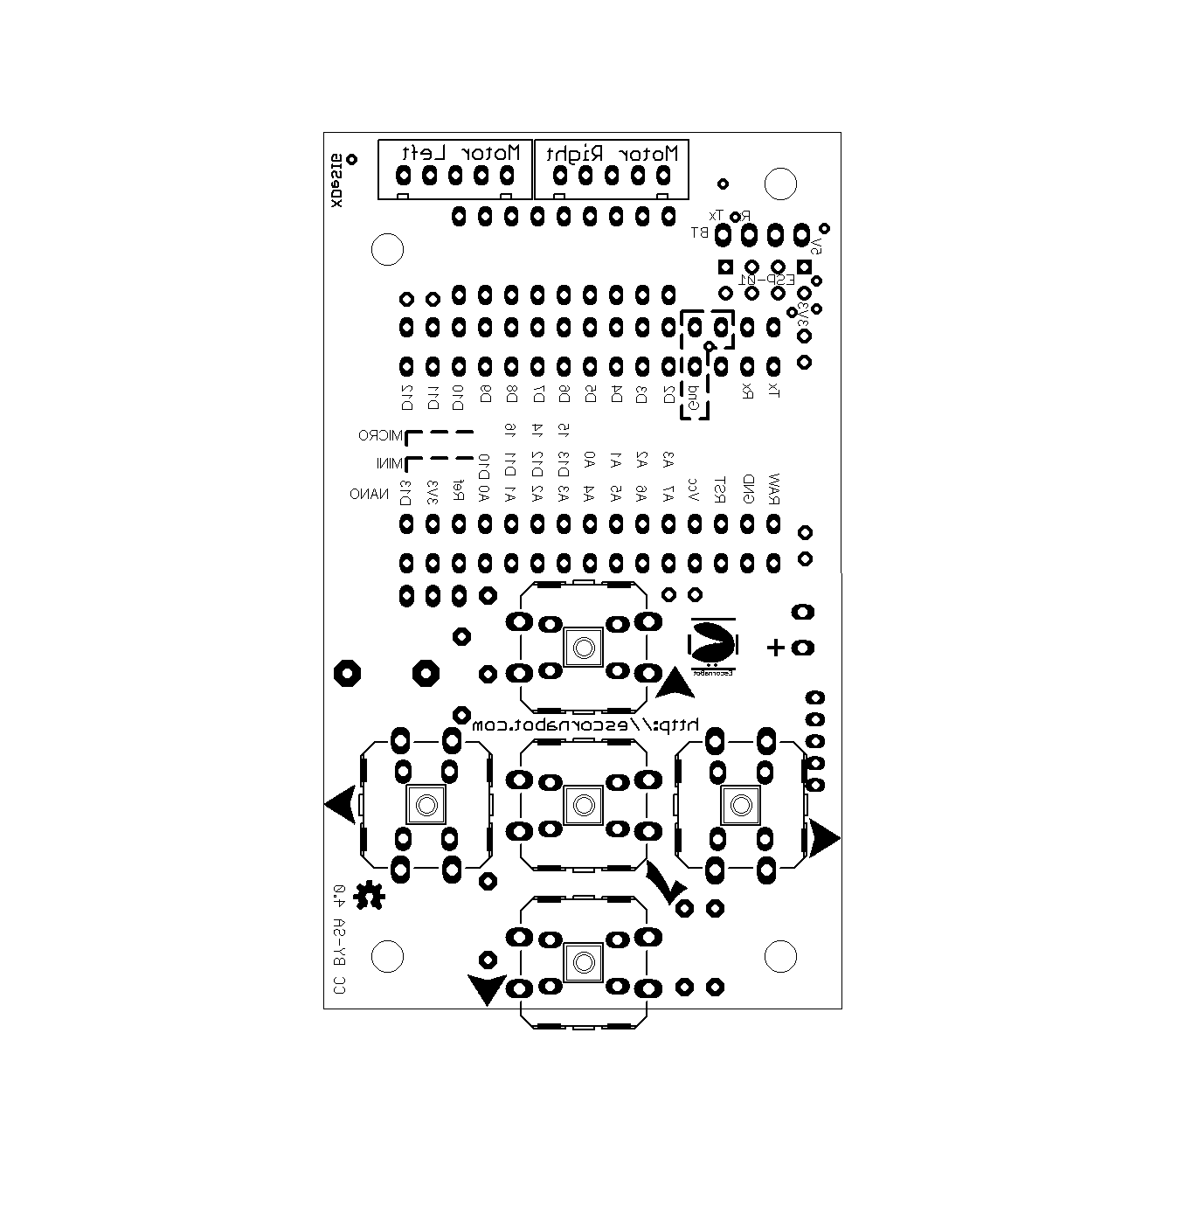
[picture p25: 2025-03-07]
Electronics/EscornaCPU/2.x/2.01/Escorna_CPU_2_01_Bott_Silk.png

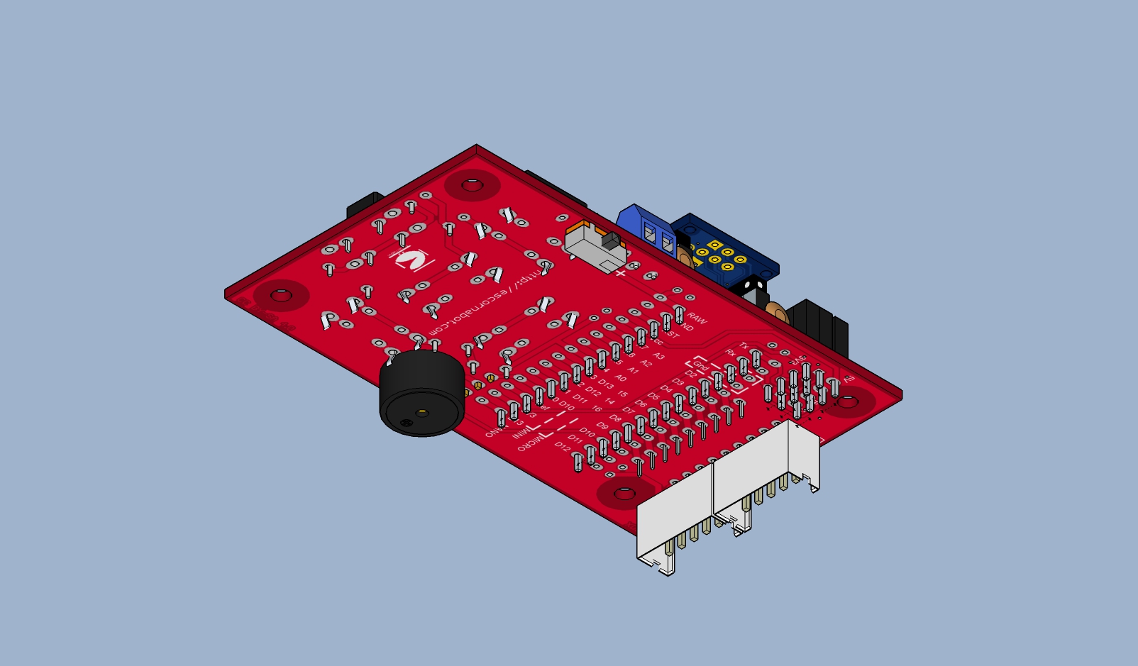
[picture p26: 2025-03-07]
Electronics/EscornaCPU/2.x/2.01/Escorna_CPU_2_01_34B.jpg

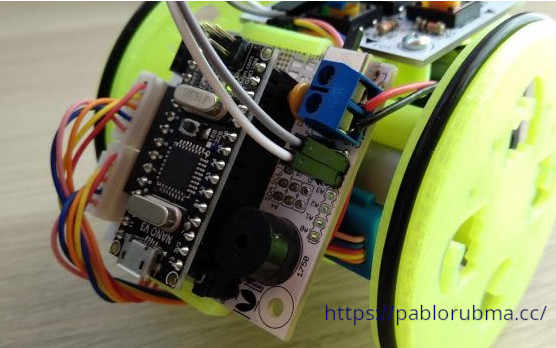
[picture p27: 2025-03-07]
Electronics/EscornaCPU/1.x/1.20/Escorna_CPU_1_20_PABLO.jpg

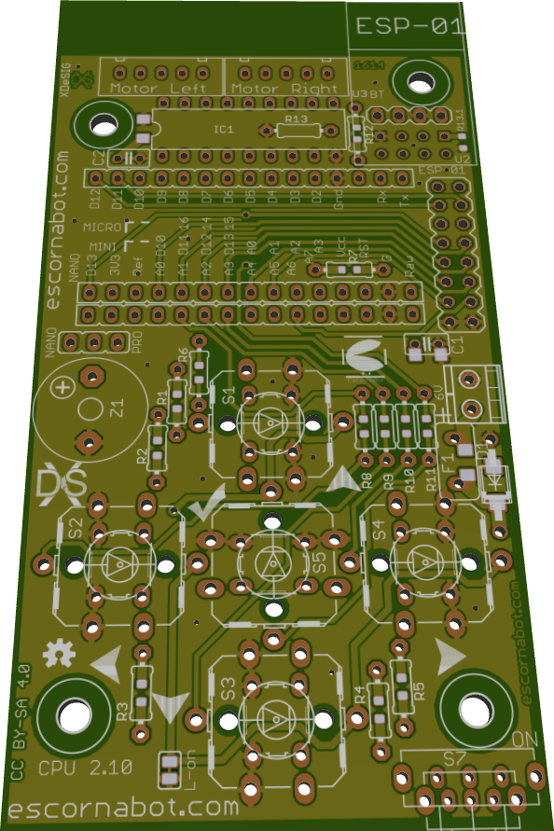
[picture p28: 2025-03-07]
Electronics/EscornaCPU/2.x/2.10/Escorna_CPU_2_10_Top.png

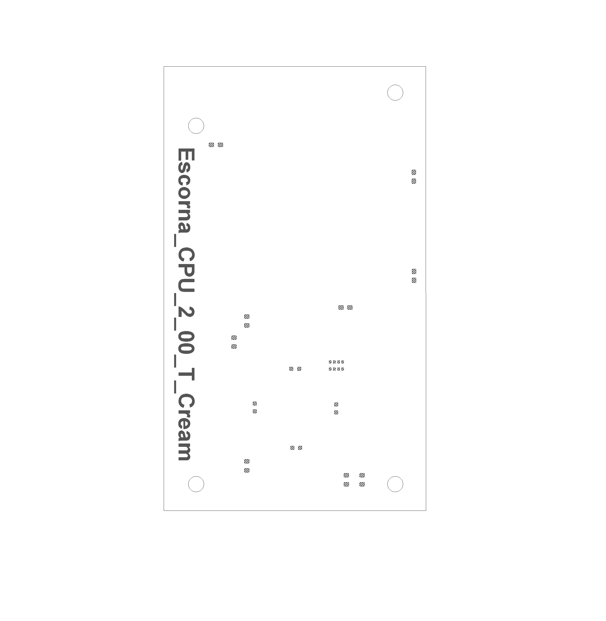
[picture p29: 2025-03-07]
Electronics/EscornaCPU/2.x/2.01/Escorna_CPU_2_01_T_Cream.png

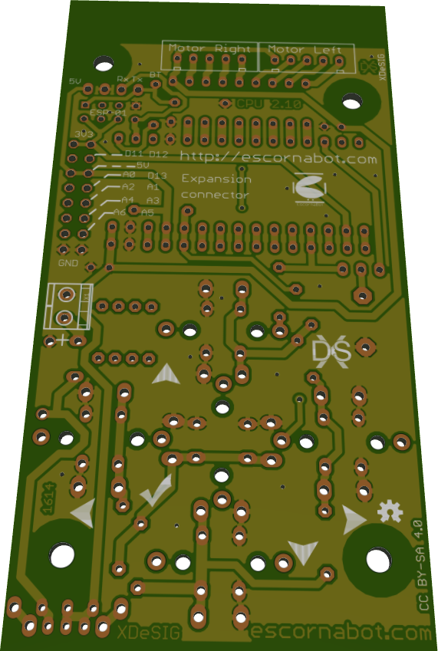
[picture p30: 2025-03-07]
Electronics/EscornaCPU/2.x/2.10/Escorna_CPU_2_10_Bottom.png

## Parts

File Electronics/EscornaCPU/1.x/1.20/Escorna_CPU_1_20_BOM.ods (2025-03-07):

Escornabot CPU 1.20
Qty | Value | Device | Package | Parts | Description | LCSC
2 | B5B-XH-A | B5B-XH-A | B5B-XH-A | XH1, XH2, Or (XH3, XH4) | HX Connector | C5306531 (https://www.lcsc.com/product-detail/Wire-To-Board-Wire-To-Wire-Connector_JST-Sales-America-B5B-XH-AM_C5306531.html)
4 | 2.54 mm 1 X 2 pin | 2 pin | 1X02 | JP1, JP2, JP3, JP4 | 2.54 mm 1 X 2 pin | C5116481 (https://www.lcsc.com/product-detail/span-style-background-color-ff0-Pin-span-Headers_ZHOURI-2-54-1-2_C5116481.html)
2 | 2.54 mm 1 X 4 header | 1 X 4 header | 2.54 mm 1 X 4 header | JP5, U3 | PIN HEADER | C2718488 (https://www.lcsc.com/product-detail/Female-Headers_BOOMELE-Boom-Precision-Elec-C2718488_C2718488.html)
1 | 2.54 mm 1 X 6 pin | 6 pin | 2.54 mm 1 X 6 pin | SV6 | 2.54 mm 1 X 6 pin | C5156615 (https://www.lcsc.com/product-detail/Pin-Headers_ZHOURI-2-54-1-6_C5156615.html)
2 | 1x15 SOCKET STRIP | 2.54 mm 1 X 15 header | 2.54 mm 1 X 15 header | SV1, SV2 | FEMALE HEADER | C124408 (https://www.lcsc.com/product-detail/Female-Headers_Ckmtw-Shenzhen-Cankemeng-B-2200S15P-A120_C124408.html)
1 | 2.54 mm 2 X 4 pin | 2.54 mm 2 X 4 pin | 2.54 mm 2 X 4 pin | U2 | FEMALE HEADER | C92271 (https://www.lcsc.com/product-detail/Female-Headers_CONNFLY-Elec-DS1023-2-4SF11_C92271.html)
1 | AK550/2 | AK550/2 | AK550/2 | X1, OR X1.1 | Screw terminal 3.5mm | C784940
1 | F/CM12P | F/CM12P | F/CM12P | Z1 | BUZZER 12mm (7mm) | C2689171 (https://www.lcsc.com/product-detail/Buzzers_S-S-SUN-1295Y-0327-45P7-6_C2689171.html)
1 | SK12D07 | SK-12D07 | SK-12D07 | S7.1 | Slide sw | C431547 (https://www.lcsc.com/product-detail/Slide-Switches_SHOU-HAN-SK12D07VG3_C431547.html)
1 | ULN2803 | ULN2803A | DIL18+ IC-18P Socket | IC1 | DRIVER ARRAY+IC Socket | C73936 + C5289488 (https://www.lcsc.com/product-detail/Darlington-Transistor-Arrays_STMicroelectronics-ULN2803A_C73936.html)
THT Option
2 | 100nF | C-EU025-025X050 | C025-025X050 | C1, C3 | CAPACITOR | C353903 (https://www.lcsc.com/product-detail/Ceramic-Disc-Capacitors_Dersonic-CC1H104ZA1PD3F5P3003_C353903.html)
4 | 10K | R-EU_0204/7 | 0204/7 | R1, R2, R4, R5 | RESISTOR | C61299 (https://www.lcsc.com/product-detail/Through-Hole-Resistors_UNI-ROYAL-Uniroyal-Elec-CFR0W4J0103A50_C61299.html)
1 | 18K | R-EU_0204/7 | 0204/7 | R3 | RESISTOR | C70811 (https://www.lcsc.com/product-detail/Through-Hole-Resistors_UNI-ROYAL-Uniroyal-Elec-CFR0W4J0183A50_C70811.html)
1 | 1N5817 | P4KEXX | DO41-10 | D1 | DIODE | C698892 (https://www.lcsc.com/product-detail/Schottky-Barrier-Diodes-SBD_Yangzhou-Yangjie-Elec-Tech-1N5817_C698892.html)
1 | PFRA.050 | FUSETE5 | TE5 | F1 | Fuse | C1562414 (https://www.lcsc.com/product-detail/Resettable-Fuses_SCHURTER-PFRA-050_C1562414.html)
SMD Option
2 | 100nF | 100nF/16 1206 | SMD 1206 | C1.1, C3.1 | CAPACITOR | C2858001 (https://www.lcsc.com/product-detail/Multilayer-Ceramic-Capacitors-MLCC-SMD-SMT_FH-Guangdong-Fenghua-Advanced-Tech-1206B104M101NT_C2858001.html)
4 | 10K | R10K | SMD 0603 | R1.1, R2.1, R4.1, R5.1 | RESISTOR | C3017715 (https://www.lcsc.com/product-detail/Chip-Resistor-Surface-Mount_VO-SCR0603J10K_C3017715.html)
1 | 18K | R18K | SMD 0603 | R3.1 | RESISTOR | C3017709 (https://www.lcsc.com/product-detail/Chip-Resistor-Surface-Mount_VO-SCR0603J18K_C3017709.html)
1 | SS14 | SS12 / SS32 | DO214 | D1.1 | SCHOTTKY BARRIER RECTIFIER | C2480 (https://www.lcsc.com/product-detail/Schottky-Barrier-Diodes-SBD_MDD-Microdiode-Electronics-SS14_C2480.html)
1 | MF200-2 | FUSETE5 | SMD 1206 | F1.1 | PTC Resettable Fuse | C89656 (https://www.lcsc.com/product-detail/Resettable-Fuses_BOURNS-MF-NSMF200-2_C89656.html)
Optional (not required, if mounting Nano Robotdyn)
1 | 1117-3.3 | ASM1117-3.3 | SOT223 | U6 | IDCHIP 1117-3.3 | C5125088 (https://www.lcsc.com/product-detail/Linear-Voltage-Regulators-LDO_IDCHIP-1117-3-3_C5125088.html)
1 | 1uF | C-EUC1206 | C1206 | C2 | CAPACITOR | C2858003 (https://www.lcsc.com/product-detail/Multilayer-Ceramic-Capacitors-MLCC-SMD-SMT_FH-Guangdong-Fenghua-Advanced-Tech-1206B105M101NT_C2858003.html)

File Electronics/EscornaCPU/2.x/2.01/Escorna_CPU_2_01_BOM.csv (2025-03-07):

Part | Value | Device | Package | Description
C1.1 | 100nF | C-EUC0603 | C0603 | CAPACITOR, European symbol
C2.1 | 100nF | C-EUC0603 | C0603 | CAPACITOR, European symbol
C3.1 | 100nF | C-EUC0603 | C0603 | CAPACITOR, European symbol
C4.1 | 10nF | C-EUC0603 | C0603 | CAPACITOR, European symbol
IC1 | ULN2803 | ULN2803A";"DIL18 | DRIVER ARRAY
JP2 |  | JP2E | PinHead 1X03 | PinHead 1X03
LED1 |  | LED_ESML0603 | LED_SML0603 | LED
LED2 |  | LED_ESML0603 | LED_SML0603 | LED
LED3 |  | LED_ESML0603 | LED_SML0603 | LED
LED4 |  | LED_ESML0603 | LED_SML0603 | LED
PH1 |  | FE15-1 | Female Header 1x15 | FEMALE HEADER
PH2 |  | FE15-1 | Female Header 1x15 | FEMALE HEADER
PH3 |  | FE15-1 | Female Header 1x15 | FEMALE HEADER
PH4 |  | FE15-1 | Female Header 1x15 | FEMALE HEADER
R1.1 | 10K | R-EU_R0603 | R0603 | RESISTOR, European symbol
R2.1 | 10K | R-EU_R0603 | R0603 | RESISTOR, European symbol
R3.1 | 10K | R-EU_R0603 | R0603 | RESISTOR, European symbol
R4.1 | 10K | R-EU_R0603 | R0603 | RESISTOR, European symbol
R5.1 | 10K | R-EU_R0603 | R0603 | RESISTOR, European symbol
RN4 | 1K | 4R-NCAY16 | CAY16 | Array Chip Resistor
S1 |  | 10-XX | B3F-10XX | OMRON SWITCH
S2 |  | 10-XX | B3F-10XX | OMRON SWITCH
S3 |  | 10-XX | B3F-10XX | OMRON SWITCH
S4 |  | 10-XX | B3F-10XX | OMRON SWITCH
S5 |  | 10-XX | B3F-10XX | OMRON SWITCH
S6 |  | SK12F14F | SK-12F14-G | Slide SWITCH PIC
U2 | ESP01 | ESP01 | FemaleHeader 2x04 | Conector for ESP8266 Wifi module
U3 |  | MA04-1 | FemaleHeader 1x04 | PIN HEADER 4 pines Female
X1 | AK550/2 | AK550/2 | AK550/2 | CONNECTOR
XH1 |  | B5B-XH-A | B5B-XH-A | CONNECTOR
XH2 |  | B5B-XH-A | B5B-XH-A | CONNECTOR
Z1 | CFG12 | CFG12 | CFG12 | Buzer 12mm

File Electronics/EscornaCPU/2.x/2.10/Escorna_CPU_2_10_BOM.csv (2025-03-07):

Part | Value | Device | Package | Description | MF | MPN | OC_FARNELL | OC_NEWARK
C1 | 100nF/16V | C-EU025-025X050 | C025-025X050 | CAPACITOR, Multilayer Ceramic Radial LEADED
C1.1 | 100nF/16V | C-EUC1206 | C1206 | CAPACITOR, SMD 3216 Metric (1206 Imperial)
C2 | 100nF/16V | C-EU025-025X050 | C025-025X050 | CAPACITOR, Multilayer Ceramic Radial LEADED
C2.1 | 100nF/16V | C-EUC1206 | C1206 | CAPACITOR, SMD 3216 Metric (1206 Imperial)
D1 | 1N5817 | SCHOTTKY-DIODE DO41 | DO41-10 | DIODE
D1.1 | M7 | SCHOTTKY-DIODE SMA | SMA | DIODE SMA
F1 | PFRA.050 | RFUSE | PFRA.050 | PTC fuses, resettable thermistors |  |  | unknown | unknown
F1.1 | PolySwitch | PTCFUSE-1206 | R1206 | PTC fuses, resettable thermistors
IC1 | ULN2803 | ULN2803A | DIL18 | DarlingtonTransistorArrays
JP1 |  | JUMPER_JP2E | 3Fx1-2,54mm | MALE HEADER 3Pins
R1 | 10K | R-EU_0204/7 | 0204/7 | RESISTOR, ¼ Watt
R1.1 | 10K | R-EU_R0603 | R0603 | RESISTOR, SMD 1608 Metric (0603 Imperial)
R2 | 10K | R-EU_0204/7 | 0204/7 | RESISTOR, ¼ Watt
R2.1 | 10K | R-EU_R0603 | R0603 | RESISTOR, SMD 1608 Metric (0603 Imperial)
R3 | 10K | R-EU_0204/7 | 0204/7 | RESISTOR, ¼ Watt
R3.1 | 10K | R-EU_R0603 | R0603 | RESISTOR, SMD 1608 Metric (0603 Imperial)
R4 | 10K | R-EU_0204/7 | 0204/7 | RESISTOR, ¼ Watt
R4.1 | 10K | R-EU_R0603 | R0603 | RESISTOR, SMD 1608 Metric (0603 Imperial)
R5 | 22K | R-EU_0204/7 | 0204/7 | RESISTOR, ¼ Watt
R5.1 | 22K | R-EU_R0603 | R0603 | RESISTOR, SMD 1608 Metric (0603 Imperial)
R6 | 1K | R-EU_0204/7 | 0204/7 | RESISTOR, ¼ Watt
R6.1 | 1K | R-EU_R0603 | R0603 | RESISTOR, SMD 1608 Metric (0603 Imperial)
R7 | 10K | R-EU_0204/7 | 0204/7 | RESISTOR, ¼ Watt
R7.1 | 10K | R-EU_R0603 | R0603 | RESISTOR, SMD 1608 Metric (0603 Imperial)
R8 | 1K | R-EU_0204/7 | 0204/7 | RESISTOR, ¼ Watt
R8.1 | 1K | R-EU_R0603 | R0603 | RESISTOR, SMD 1608 Metric (0603 Imperial)
R9 | 1K | R-EU_0204/7 | 0204/7 | RESISTOR, ¼ Watt
R9.1 | 1K | R-EU_R0603 | R0603 | RESISTOR, SMD 1608 Metric (0603 Imperial)
R10 | 100 Ohm | R-EU_0204/7 | 0204/7 | RESISTOR, ¼ Watt
R10.1 | 100 Ohm | R-EU_R0603 | R0603 | RESISTOR, SMD 1608 Metric (0603 Imperial)
R11 | 1K | R-EU_0204/7 | 0204/7 | RESISTOR, ¼ Watt
R11.1 | 1K | R-EU_R0603 | R0603 | RESISTOR, SMD 1608 Metric (0603 Imperial)
R12 | 10K | R-EU_0204/7 | 0204/7 | RESISTOR, ¼ Watt
R12.1 | 10K | R-EU_R0603 | R0603 | RESISTOR, SMD 1608 Metric (0603 Imperial)
R13 | 18K | R-EU_0204/7 | 0204/7 | RESISTOR, ¼ Watt
R13.1 | 18K | R-EU_R0603 | R0603 | RESISTOR, SMD 1608 Metric (0603 Imperial)
S1.1 | B3F-9XXX | SWITCH-OMRON_B3F-9XXX | B3F-9XXX | OMRON SWITCH / Led
S1.2 | B3F-9XXX | SWITCH-OMRON_B3F-9XXX | B3F-9XXX | OMRON SWITCH / Led
S1.3 | B3F-9XXX | SWITCH-OMRON_B3F-9XXX | B3F-9XXX | OMRON SWITCH / Led
S1.4 | B3F-9XXX | SWITCH-OMRON_B3F-9XXX | B3F-9XXX | OMRON SWITCH / Led
S1.5 | B3F-9XXX | SWITCH-OMRON_B3F-9XXX | B3F-9XXX | OMRON SWITCH / Led
S1 |  | 10-XX | B3F-10XX | OMRON SWITCH 6mm |  | B3F-1000 | 176432 | 36M3542
S2 |  | 10-XX | B3F-10XX | OMRON SWITCH 6mm |  | B3F-1000 | 176432 | 36M3542
S3 |  | 10-XX | B3F-10XX | OMRON SWITCH 6mm |  | B3F-1000 | 176432 | 36M3542
S4 |  | 10-XX | B3F-10XX | OMRON SWITCH 6mm |  | B3F-1000 | 176432 | 36M3542
S5 |  | 10-XX | B3F-10XX | OMRON SWITCH 6mm |  | B3F-1000 | 176432 | 36M3542
S7 |  | SK12F14F | SK-12F14 | SWITCH (http://www.xiejia.com.hk) DH 17.117
S7.1 |  | SK12D07 | SK-12D07 | SWITCH (http://bit.ly/1N7X7Jb)
SV1 |  | MA08-2 | MA08-2 | PIN HEADER |  |  | unknown | unknown
SV2 |  | CON-LSTA_FE15-1 | 15Fx1-2,54mm | FEMALE HEADER 15Pins |  |  | unknown | unknown
SV3 |  | CON-LSTA_FE15-1 | 15Fx1-2,54mm | FEMALE HEADER 15Pins |  |  | unknown | unknown
SV4 |  | CON-LSTA_FE15-1 | 15Fx1-2,54mm | FEMALE HEADER 15Pins |  |  | unknown | unknown
U2 | ESP01 | Con ESP01 | 4Fx1-2,54mm | ESP8266 Wifi module 01 connector 2x4Fx1-2,54mm
U3 |  | MA04-1 | 4Fx1-2,54mm | PIN HEADER |  |  | unknown | unknown
X1 | AK550/2 | AK550/2 | AK550/2 | CONNECTOR Pin Spacing 3.5mm |  |  | unknown | unknown
X1.1 | AK550/2 | AK550/2 | AK550/2 | CONNECTOR Pin Spacing 3.5mm |  |  | unknown | unknown
XH1 |  | B5B-XH-A | B5B-XH-A | CONNECTOR HEADER XH TOP 5POS
XH2 |  | B5B-XH-A | B5B-XH-A | CONNECTOR HEADER XH TOP 5POS
Z1 | CFG12 | F/CM12P | F/CM12P | Buzzer, 5V 12mm |  |  | unknown | unknown

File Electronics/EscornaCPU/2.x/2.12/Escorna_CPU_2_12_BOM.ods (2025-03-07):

 |  |  |  |  |  | “XDESIG”
Escornabot CPU 2.12
Qty | Value | Device | Package | Parts | Description | LCSC
5 | B3F-4055 | B3F-4055 | B3F-4055 | S1.1, S2.1, S3.1, S4.1, S5.1 | OMRON SWITCH | C84931 (https://www.lcsc.com/product-detail/Tactile-Switches_Omron-Electronics-B3F-4055_C84931.html)
4 | B5B-XH-A | B5B-XH-A | B5B-XH-A | XH1, XH2, or (XH3, XH4) | HX Connector | C5306531 (https://www.lcsc.com/product-detail/Wire-To-Board-Wire-To-Wire-Connector_JST-Sales-America-B5B-XH-AM_C5306531.html)
2 | 2.54 mm 1 X 15 header | 2.54 mm 1 X 15 header | 2.54 mm 1 X 15 header | SV2, SV3 | FEMALE HEADER | C124408 (https://www.lcsc.com/product-detail/Female-Headers_Ckmtw-Shenzhen-Cankemeng-B-2200S15P-A120_C124408.html)
1 | 2.54 mm 2 X 4 pin | 2.54 mm 2 X 4 pin | 2.54 mm 2 X 4 pin | U2 | FEMALE HEADER | C92271 (https://www.lcsc.com/product-detail/Female-Headers_CONNFLY-Elec-DS1023-2-4SF11_C92271.html)
1 | 2.54 mm 1 X 2 pin | 2.54 mm 1 X 2 | 2.54 mm 1 X 2 | JP1 | JUMPER with cap | C5116481 (https://www.lcsc.com/product-detail/span-style-background-color-ff0-Pin-span-Headers_ZHOURI-2-54-1-2_C5116481.html)
2 | 2.54 mm 1 X 4 header | MA04-1 | 2.54 mm 1 X 4 header | SV4, U3 | PIN HEADER | C2718488 (https://www.lcsc.com/product-detail/Female-Headers_BOOMELE-Boom-Precision-Elec-C2718488_C2718488.html)
2 | AK550/2 | AK550/2 | AK550/2 | X1, X1.1 | Screw terminal 3.5mm | C784940
1 | SK12D07 | SK-12D06 | SK-12D07 | S7.1 | Slide sw | C431547 (https://www.lcsc.com/product-detail/Slide-Switches_SHOU-HAN-SK12D07VG3_C431547.html)
1 | ULN2803 | ULN2803A | DIL18 | IC1 | DRIVER ARRAY | C73936 (https://www.lcsc.com/product-detail/Darlington-Transistor-Arrays_STMicroelectronics-ULN2803A_C73936.html)
1 | F/CM12P | F/CM12P | F/CM12P | SG1 | BUZZER 12mm (7mm) | C2689171 (https://www.lcsc.com/product-detail/Buzzers_S-S-SUN-1295Y-0327-45P7-6_C2689171.html)
THT Option
1 | BLUE | LED3MM | LED3MM | LED1 | LED 3mm | C2895474 (https://www.lcsc.com/product-detail/Light-Emitting-Diodes-LED_XINGLIGHT-XL-302UBD_C2895474.html)
1 | RED | LED3MM | LED3MM | LED2 | LED 3mm | C99771 (https://www.lcsc.com/product-detail/Light-Emitting-Diodes-LED_Everlight-Elec-204-10SURD-S530-A3-L_C99771.html)
1 | YELOW | LED3MM | LED3MM | LED3 | LED 3mm | C409800 (https://www.lcsc.com/product-detail/Light-Emitting-Diodes-LED_MEIHUA-MHL3014UYTD_C409800.html)
1 | GREEN | LED3MM | LED3MM | LED4 | LED 3mm | C568935 (https://www.lcsc.com/product-detail/Light-Emitting-Diodes-LED_HONGLITRONIC-Hongli-Zhihui-HONGLITRONIC-HL-304H3GD_C568935.html)
2 | 100nF | C-EU025-025X050 | C025-025X050 | C1, C2 | CAPACITOR | C353903 (https://www.lcsc.com/product-detail/Ceramic-Disc-Capacitors_Dersonic-CC1H104ZA1PD3F5P3003_C353903.html)
1 | 22K | R-EU_0204/7 | 0204/7 | R5 | RESISTOR | C61301 (https://www.lcsc.com/product-detail/Through-Hole-Resistors_UNI-ROYAL-Uniroyal-Elec-CFR0W4J0223A50_C61301.html)
8 | 10K | R-EU_0204/7 | 0204/7 | R1, R2, R3, R4, R7, R11, R12, R14 | RESISTOR | C61299 (https://www.lcsc.com/product-detail/Through-Hole-Resistors_UNI-ROYAL-Uniroyal-Elec-CFR0W4J0103A50_C61299.html)
1 | 18K | R-EU_0204/7 | 0204/7 | R13 | RESISTOR | C70811 (https://www.lcsc.com/product-detail/Through-Hole-Resistors_UNI-ROYAL-Uniroyal-Elec-CFR0W4J0183A50_C70811.html)
4 | 1K | R-EU_0204/7 | 0204/7 | R6, R8, R9, R10 | RESISTOR | C66649 (https://www.lcsc.com/product-detail/Through-Hole-Resistors_UNI-ROYAL-Uniroyal-Elec-CFR0W4J0102A50_C66649.html)
1 | 1N5817 | P4KEXX | DO41-10 | D1 | DIODE | C698892 (https://www.lcsc.com/product-detail/Schottky-Barrier-Diodes-SBD_Yangzhou-Yangjie-Elec-Tech-1N5817_C698892.html)
1 | PFRA.050 | FUSETE5 | TE5 | F1 | Fuse | C1562414 (https://www.lcsc.com/product-detail/Resettable-Fuses_SCHURTER-PFRA-050_C1562414.html)
SMD Option
1 | BLUE | LED 0603 | SMD 0603 | LED1.1 | LED 0603 | C434421 (https://www.lcsc.com/product-detail/Light-Emitting-Diodes-LED_Yongyu-Photoelectric-SZYY0603B_C434421.html)
1 | RED | LED 0603 | SMD 0603 | LED2.1 | LED 0603 | C434419 (https://www.lcsc.com/product-detail/Light-Emitting-Diodes-LED_Yongyu-Photoelectric-SZYY0603R_C434419.html)
1 | YELOW | LED 0603 | SMD 0603 | LED3.1 | LED 0603 | C434424 (https://www.lcsc.com/product-detail/Light-Emitting-Diodes-LED_Yongyu-Photoelectric-SZYY0603Y_C434424.html)
1 | GREEN | LED 0603 | SMD 0603 | LED4.1 | LED 0603 | C434420 (https://www.lcsc.com/product-detail/Light-Emitting-Diodes-LED_Yongyu-Photoelectric-SZYY0603G_C434420.html)
2 | 100nF | 100nF/16 1206 | SMD 1206 | C1.1, C2.1 | CAPACITOR | C2858001 (https://www.lcsc.com/product-detail/Multilayer-Ceramic-Capacitors-MLCC-SMD-SMT_FH-Guangdong-Fenghua-Advanced-Tech-1206B104M101NT_C2858001.html)
1 | 22K | R22K | SMD 0603 | R5.1 | RESISTOR | C3016353 (https://www.lcsc.com/product-detail/Chip-Resistor-Surface-Mount_VO-SCR0603F22K_C3016353.html)
8 | 10K | R10K | SMD 0603 | R1.1, R2.1, R3.1, R4.1, R7.1, R11.1, R12.1, R14.1 | RESISTOR | C3017715 (https://www.lcsc.com/product-detail/Chip-Resistor-Surface-Mount_VO-SCR0603J10K_C3017715.html)
1 | 18K | R18K | SMD 0603 | R13.1 | RESISTOR | C3017709 (https://www.lcsc.com/product-detail/Chip-Resistor-Surface-Mount_VO-SCR0603J18K_C3017709.html)
4 | 1K | R1K | SMD 0603 | R6.1, R8.1, R9.1, R10.1 | RESISTOR | C3017736 (https://www.lcsc.com/product-detail/Chip-Resistor-Surface-Mount_VO-SCR0603J1K_C3017736.html)
1 | SS14 | SS12 / SS32 | DO214 | D1.1 | SCHOTTKY BARRIER RECTIFIER | C2480 (https://www.lcsc.com/product-detail/Schottky-Barrier-Diodes-SBD_MDD-Microdiode-Electronics-SS14_C2480.html)
1 | MF200-2 | FUSETE5 | SMD 1206 | F1.1 | PTC Resettable Fuse | C89656 (https://www.lcsc.com/product-detail/Resettable-Fuses_BOURNS-MF-NSMF200-2_C89656.html)
Optional (not required, if mounting Nano Robotdyn)
1 | 1117-3.3 | ASM1117-3.3 | SOT223 | U6 | IDCHIP 1117-3.3 | C5125088 (https://www.lcsc.com/product-detail/Linear-Voltage-Regulators-LDO_IDCHIP-1117-3-3_C5125088.html)
1 | 1uF | C-EUC1206 | C1206 | C1.2 | CAPACITOR | C2858003 (https://www.lcsc.com/product-detail/Multilayer-Ceramic-Capacitors-MLCC-SMD-SMT_FH-Guangdong-Fenghua-Advanced-Tech-1206B105M101NT_C2858003.html)

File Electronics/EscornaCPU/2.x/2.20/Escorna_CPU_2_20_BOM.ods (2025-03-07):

Qty | Value | Device | Package | Parts | Description
4 | B5B-XH-A | B5B-XH-A | B5B-XH-A | XH1, XH2, XH3, XH4
2 | JP1E | JP1E | 1X02 | JP1, JP2 | Jumper
2 | 1x15 SOCKET STRIP | CON-LSTA_FE15-1 | CON-LSTA_FE15 | SV2, SV3 | FEMALE HEADER
4 | MA04-1 | MA04-1 | MA04-1 | U1, U3, U4, U5 | PIN HEADER
2 | MA06-1 | MA06-1 | MA06-1 | SV4, SV5 | PIN HEADER
1 | MA08-2 | MA08-2 | MA08-2 | SV1 | PIN HEADER
2 | 100nF | C-EU025-025X050 | C025-025X050 | C1, C2 | CAPACITOR
2 | 100nF | C-EUC0603K | C0603K | C1.1, C2.1 | CAPACITOR
7 | 10K | R-EU_0204/7 | 0204/7 | R1, R2, R3, R4, R10, R11, R13 | RESISTOR
7 | 10K | R-EU_R0603 | R0603 | R1.1, R2.1, R3.1, R4.1, R10.1, R11.1, R13.1 | RESISTOR
1 | 18K | R-EU_0204/7 | 0204/7 | R12 | RESISTOR
1 | 18K | R-EU_R0603 | R0603 | R12.1 | RESISTOR
4 | 1K | R-EU_0204/7 | 0204/7 | R6, R7, R8, R9 | RESISTOR
4 | 1K | R-EU_R0603 | R0603 | R6.1, R7.1, R8.1, R9.1 | RESISTOR
1 | 1uF | C-EUC0603K | C0603K | C1.2 | CAPACITOR
1 | 22K | R-EU_0204/7 | 0204/7 | R5 | RESISTOR
1 | 22K | R-EU_R0603 | R0603 | R5.1 | RESISTOR
2 | AK550/2 | AK550/2 | AK550/2 | X1, X1.1 | CONNECTOR
1 | AMS1117-3.3 | AMS1117-3.3 | SOT223 | U6 | Advanced Monolithic Systems
5 | B3F-1050 | 10-XX | B3F-10XX | S1, S2, S3, S4, S5 | OMRON SWITCH
5 | B3F-4050 | 40-XX | B3F-40XX | S1.1, S2.1, S3.1, S4.1, S5.1 | OMRON SWITCH
1 | CFG12 | F/CM12P | F/CM12P | Z1 | BUZZER
1 | ESP01 | ESP01 | ESP01 | U2 | ESP8266 Wifi module 01
1 | Blue | LED3MM | LED3MM | LED1 | LED
1 | Blue | LEDCHIPLED_0603 | CHIPLED_0603 | LED1.1 | LED
1 | Reed | LED3MM | LED3MM | LED2 | LED
1 | Reed | LEDCHIPLED_0603 | CHIPLED_0603 | LED2.1 | LED
1 | Green | LED3MM | LED3MM | LED4 | LED
1 | Green | LEDCHIPLED_0603 | CHIPLED_0603 | LED4.1 | LED
1 | Orange | LED3MM | LED3MM | LED3 | LED
1 | Orang | LEDCHIPLED_0603 | CHIPLED_0603 | LED3.1 | LED
1 | 1N5817 | P4KEXX | DO41-10 | D1 | DIODE
1 | M7 | SCHOTTKY-DIODESMA | SMA | D1.1 | Schottky Diode
1 | PFRA.050 | FUSETE5 | TE5 | F1 | Fuse
1 | PolySwitch | PTCFUSE-1206 | R1206 | F1.1 | PTC fuses, resettable thermistors
1 | SK12D07 | ESCORNA_SK12F14D | ESCORNA_SK-12D07 | S7.1
1 | SK12F14 | ESCORNA_SK12F14F | ESCORNA_SK-12F14-G | S7
1 | ULN2803 | ULN2803A | DIL18 | IC1 | DRIVER ARRAY
Yelow = SMD components

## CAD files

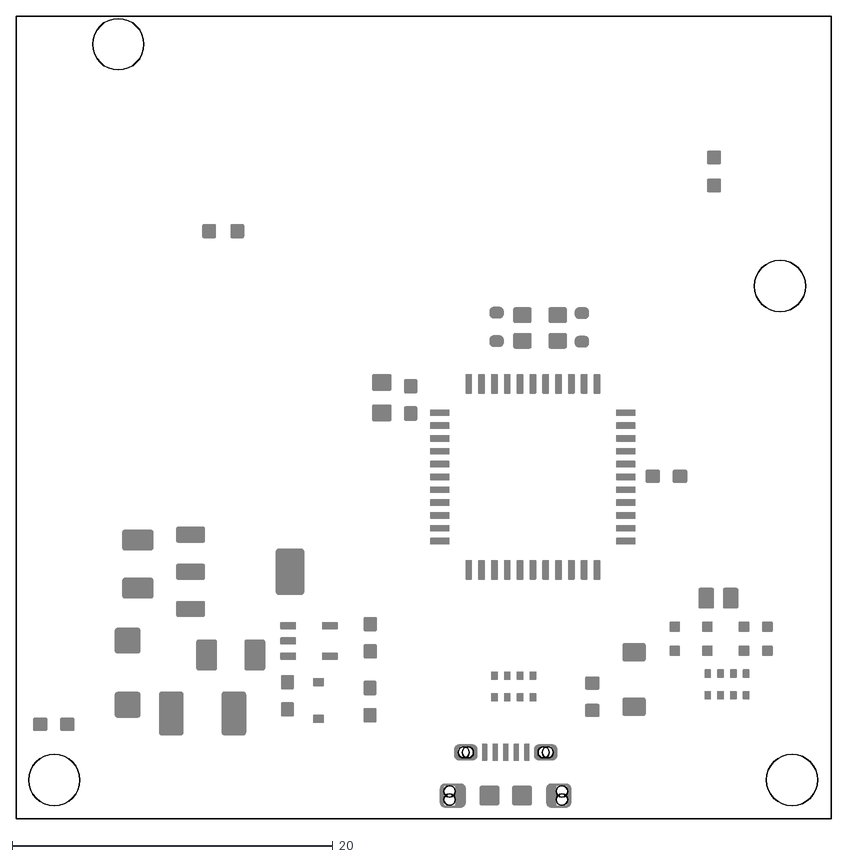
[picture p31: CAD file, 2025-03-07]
Electronics/Cervus/cervus_2_0_TCream.dxf
50.8 x 50.1

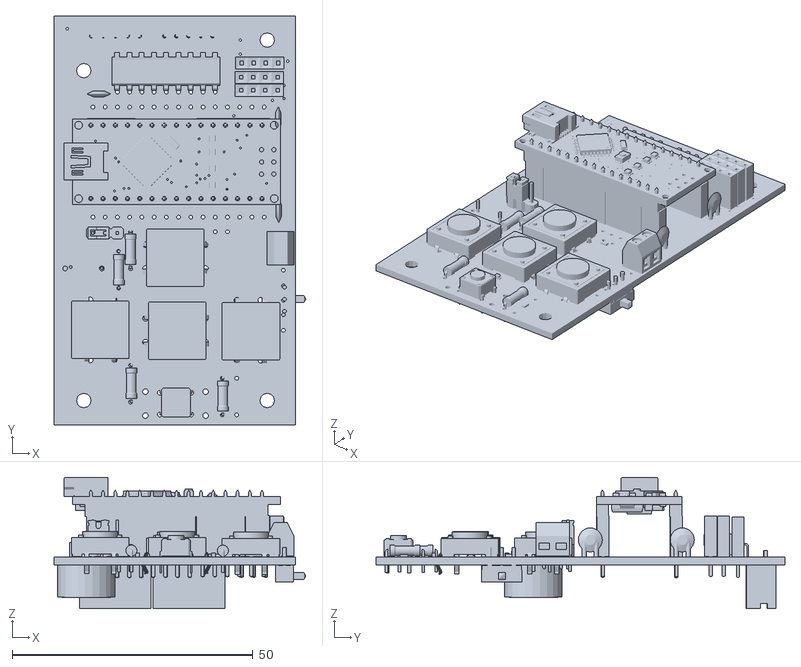
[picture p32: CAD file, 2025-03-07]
Electronics/EscornaCPU/2.x/2.01/Escorna_CPU_2_01_3D.stl
52.3 x 85.0 x 27.2

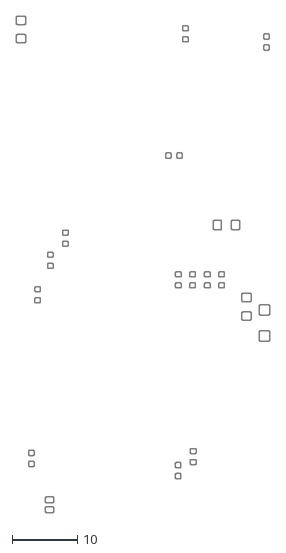
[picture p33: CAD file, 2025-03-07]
Electronics/EscornaCPU/2.x/2.10/Escorna_CPU_2_10_Cream.dxf
38.9 x 76.3

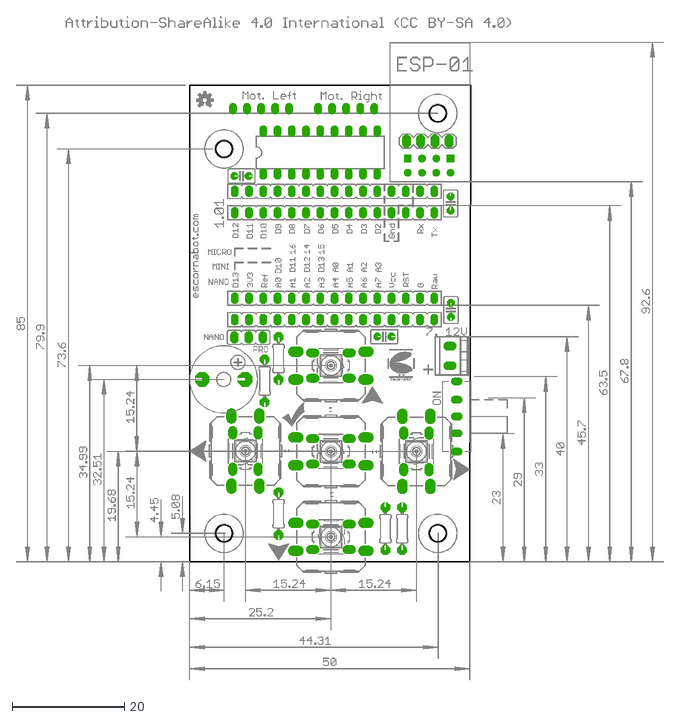
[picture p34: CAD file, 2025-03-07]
Electronics/EscornaCPU/2.x/2.01/Escorna_CPU_2_01_measures.dxf
115.5 x 118.4

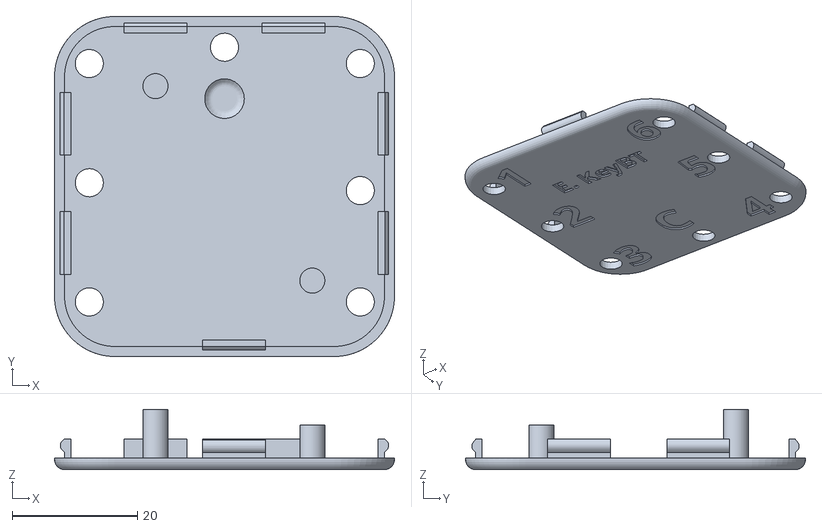
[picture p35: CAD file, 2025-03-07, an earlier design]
Electronics/E_KEY/E_KEY_BT/3D/Tapa_E_Key_BT.stl
54.2 x 54.2 x 9.60

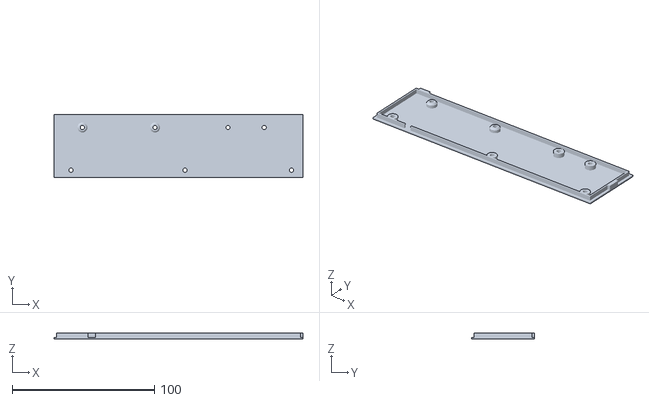
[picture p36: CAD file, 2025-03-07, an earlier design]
Electronics/E_KEY/E_KEY_FICHA/3D/E_KEY_T_V_CaseB_6F.stl
175.0 x 44.0 x 4.00

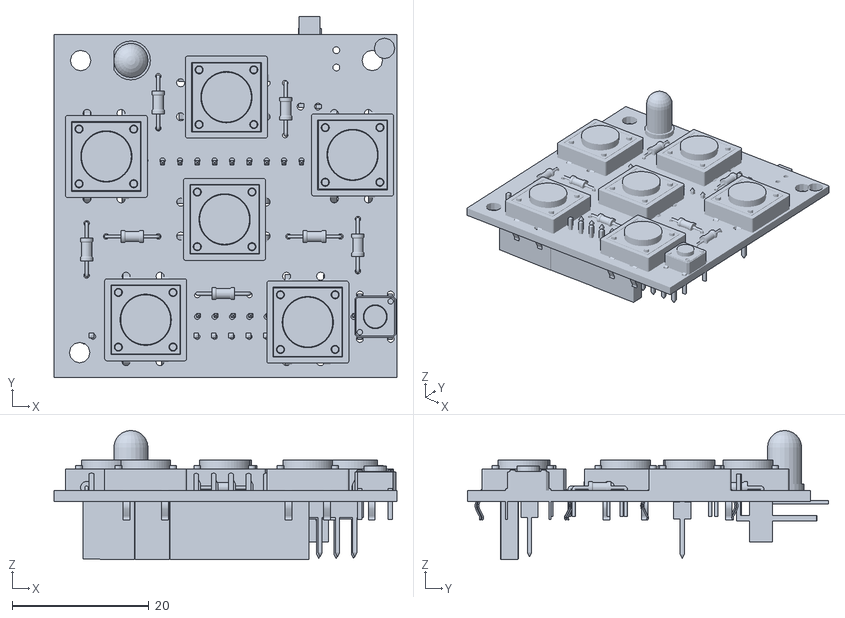
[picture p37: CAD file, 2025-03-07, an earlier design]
Electronics/E_KEY/E_KEYPAD/E_KEYPAD_2.0D/Escorna_Shield_botoneira_2_0D.stl
50.2 x 52.8 x 18.9

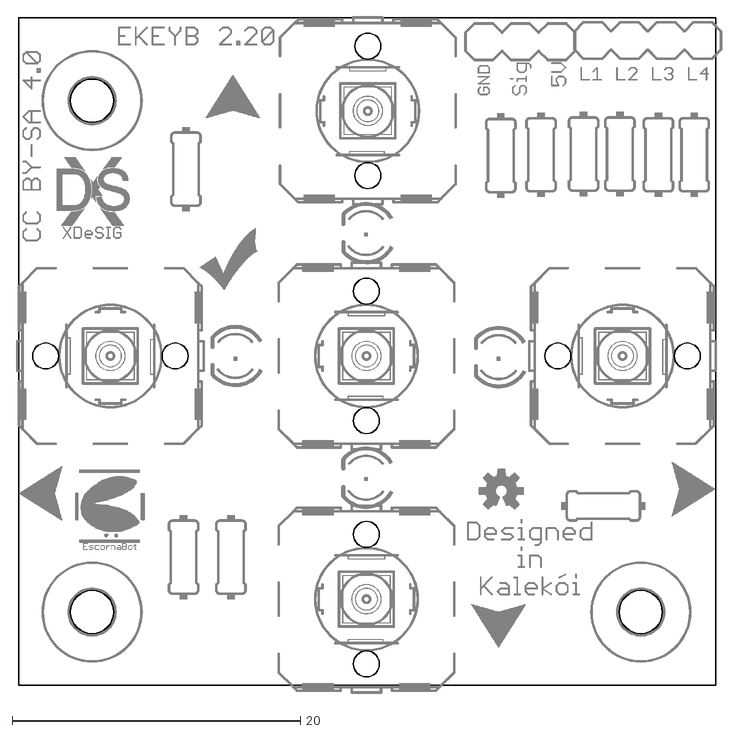
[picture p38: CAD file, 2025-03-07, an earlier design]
Electronics/E_KEY/E_KEYPAD/E_KEYPAD_2.20/E_KEYPAD_2_2_top.dxf
49.0 x 47.0

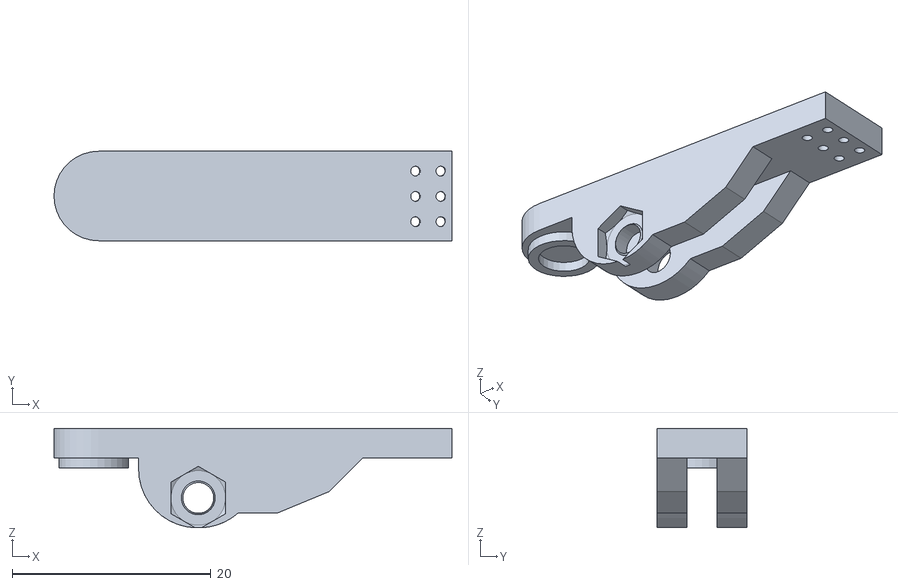
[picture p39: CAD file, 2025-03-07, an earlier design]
Electronics/EscornaCPU/2.x/2.40/3D/Pinza_ICSP_Sup.stl
40.0 x 9.00 x 10.0

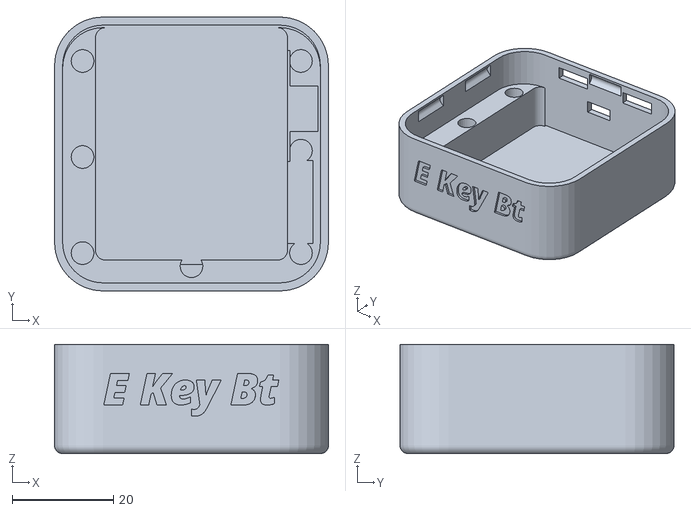
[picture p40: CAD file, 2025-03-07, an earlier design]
Electronics/E_KEY/E_KEY_BT/3D/Base_E_Key_BT.stl
54.2 x 54.2 x 21.6

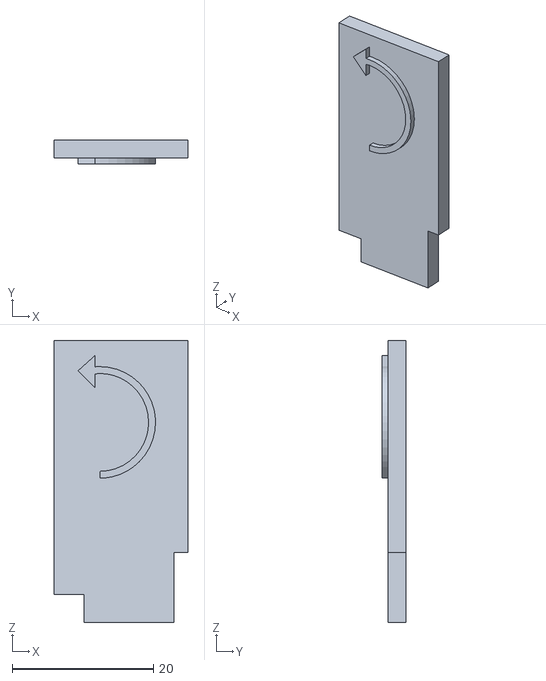
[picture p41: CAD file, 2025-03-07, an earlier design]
Electronics/E_KEY/E_KEY_FICHA/3D/E_KEY_V_F_e.stl
19.0 x 3.45 x 40.0

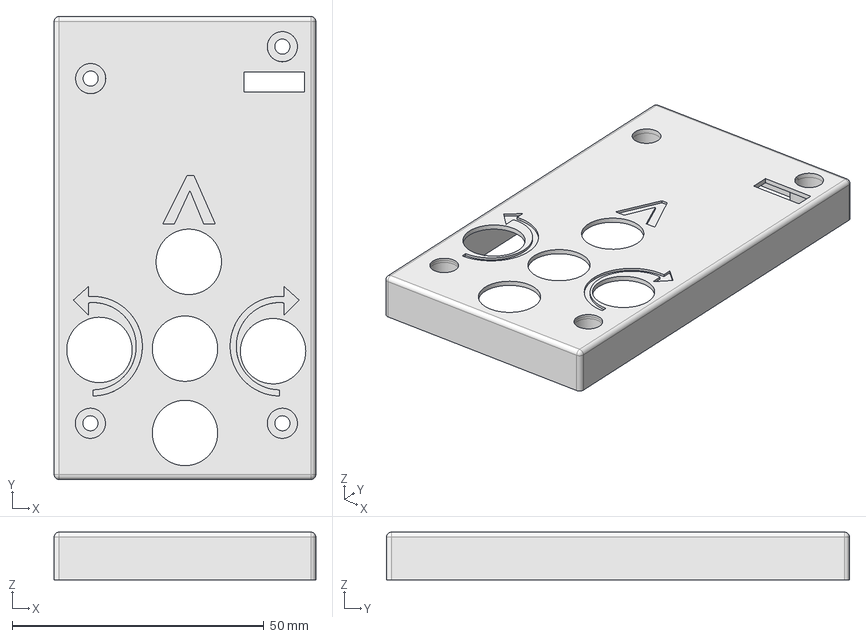
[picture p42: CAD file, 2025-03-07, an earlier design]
Electronics/EscornaCPU/2.x/2.40/3D/Tapa_2_40.FCStd
52.0 x 92.0 x 9.50 mm

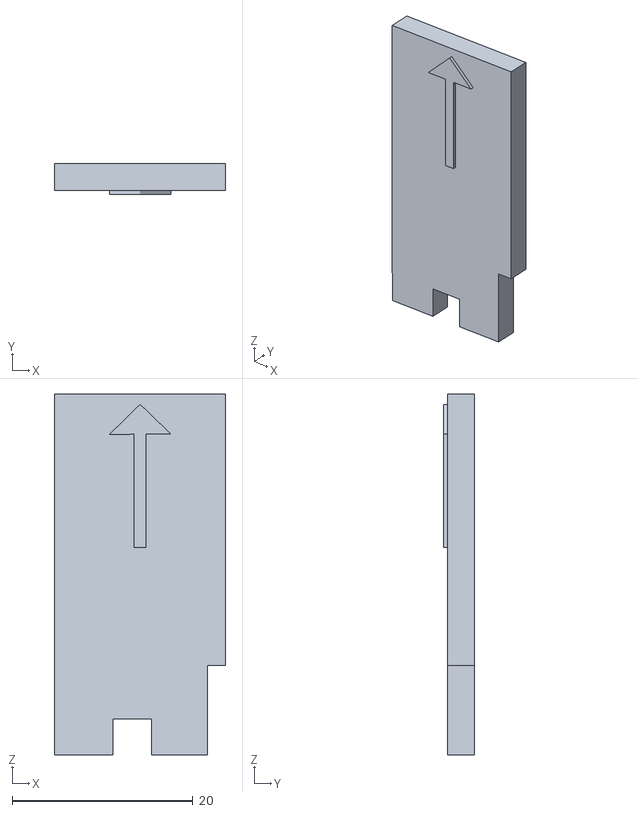
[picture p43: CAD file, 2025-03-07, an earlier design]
Electronics/E_KEY/E_KEY_FICHA/3D/E_KEY_T_V_F_s.stl
19.0 x 3.46 x 40.0

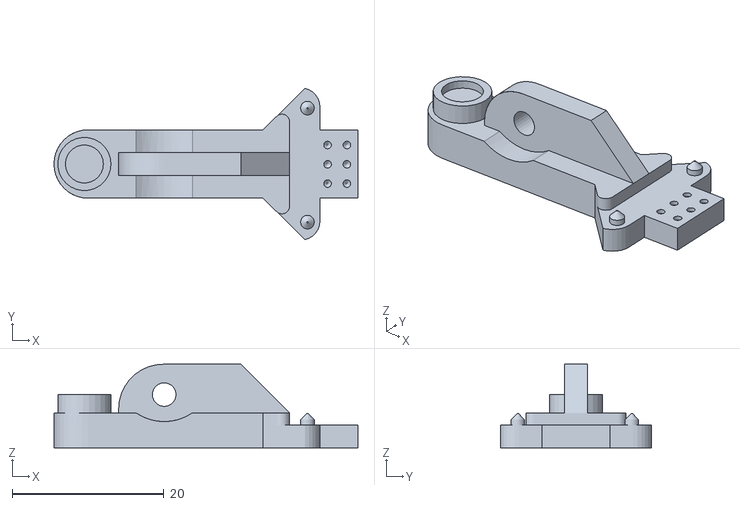
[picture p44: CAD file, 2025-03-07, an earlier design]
Electronics/EscornaCPU/2.x/2.40/3D/Pinza_ICSP_inf.stl
40.0 x 19.9 x 11.0

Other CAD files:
Electronics/E_KEY/E_KEY_FICHA/3D/E_KEY_V_F_n.stl
Electronics/E_KEY/E_KEY_FICHA/3D/E_KEY_T_V_F_n.stl
Electronics/E_KEY/E_KEY_FICHA/3D/E_KEY_T_V_CaseT_6F.stl
Electronics/E_KEY/E_KEY_FICHA/3D/E_KEY_T_V_F_w.stl
Electronics/E_KEY/E_KEY_FICHA/3D/E_KEY_T_V_6_TAB.FCStd
Electronics/E_KEY/E_KEY_FICHA/3D/E_KEY_T_V_F_e.stl
Electronics/E_KEY/E_KEY_FICHA/3D/E_KEY_V_F_s.stl
Electronics/E_KEY/E_KEY_FICHA/3D/E_KEY_V_F_w.stl

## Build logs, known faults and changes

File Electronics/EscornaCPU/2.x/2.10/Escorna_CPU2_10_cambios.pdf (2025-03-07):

## ESCORNA CPU 2,10

Cambiase a entrada do Teclado a “A7” con pullup externo.

Todos os compoñentes poden ser:
SMD (Surface Mount Device). (https://es.wikipedia.org/wiki/Tecnolog%C3%ADa_de_montaje_superficial) ou
THT (through hole) (https://es.wikipedia.org/wiki/Tecnolog%C3%ADa_de_agujeros_pasantes)

Liña de TX en 3,3V para non fastidiar o ESP8266.

Protección contra inversión por díodo Anti-paralelo (pasante ou SMD) e PolySwitch fusible rearmable.

Cambio de posición do Interruptor,

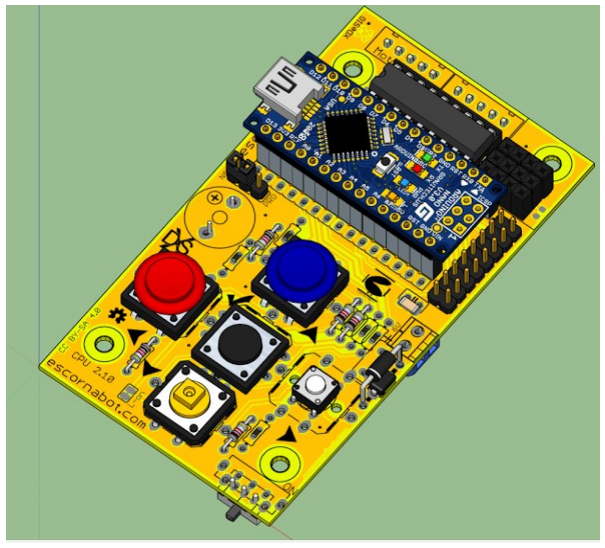
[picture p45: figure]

compatible con dous tamaños: SK-12D07 e SK-12F14

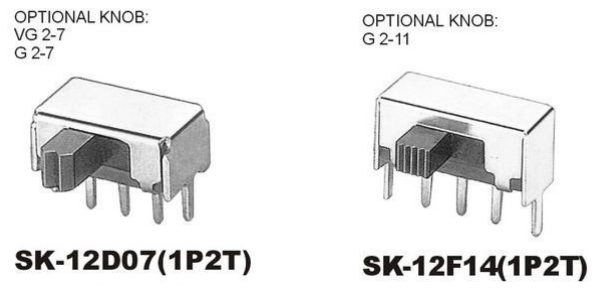
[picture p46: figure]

As teclas compatibles con Tactile Switches de 6mm 12 mm e 12mm con led (inclúe buratos de polarización)

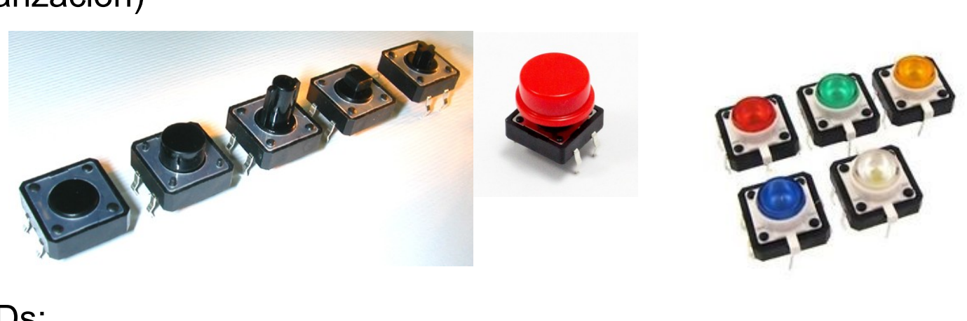
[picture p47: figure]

Asignación LEDs:

UP-A0, RIGHT-A3, DOWN-A2, LEFT-A1, GO-D13

Os leds poden desconectarse mediante o corte dunha pequena pista-Jumper, para poder utilizar esas saídas para outras cousas. (reconectanse con unha pequena soldadura), ou quitando a resistencia correspondente.

XDeSIG

Aparece o conector de expansión: dobre tira de 2,54mm

3V3 3V3
D12 D11
5V 5V
D13 A0
A1 | A2
A3 | A4
A5 | A6
GND GND

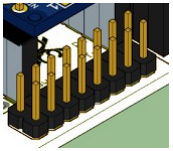
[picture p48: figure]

Eliminase un dos conectores EscornaShield (desuso).

Continua o conector SV4 (D13 – RAW) ( ampliar conexións)

O Buzer, os conectores de alimentación e motores poden conectarse por ambas caras.

Os buratos de suxeición continúan na mesma posición. (a placa ampliase 5,1mm cara atrás ).

Compatible con unha cara EscornaBot funcional (sen Leds e sinais do conector de expansión) .

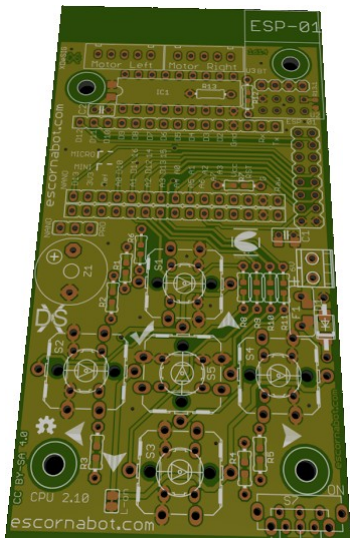
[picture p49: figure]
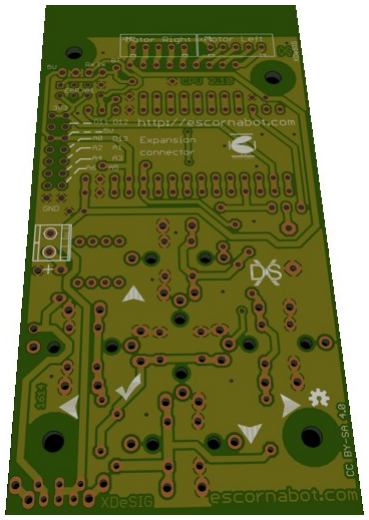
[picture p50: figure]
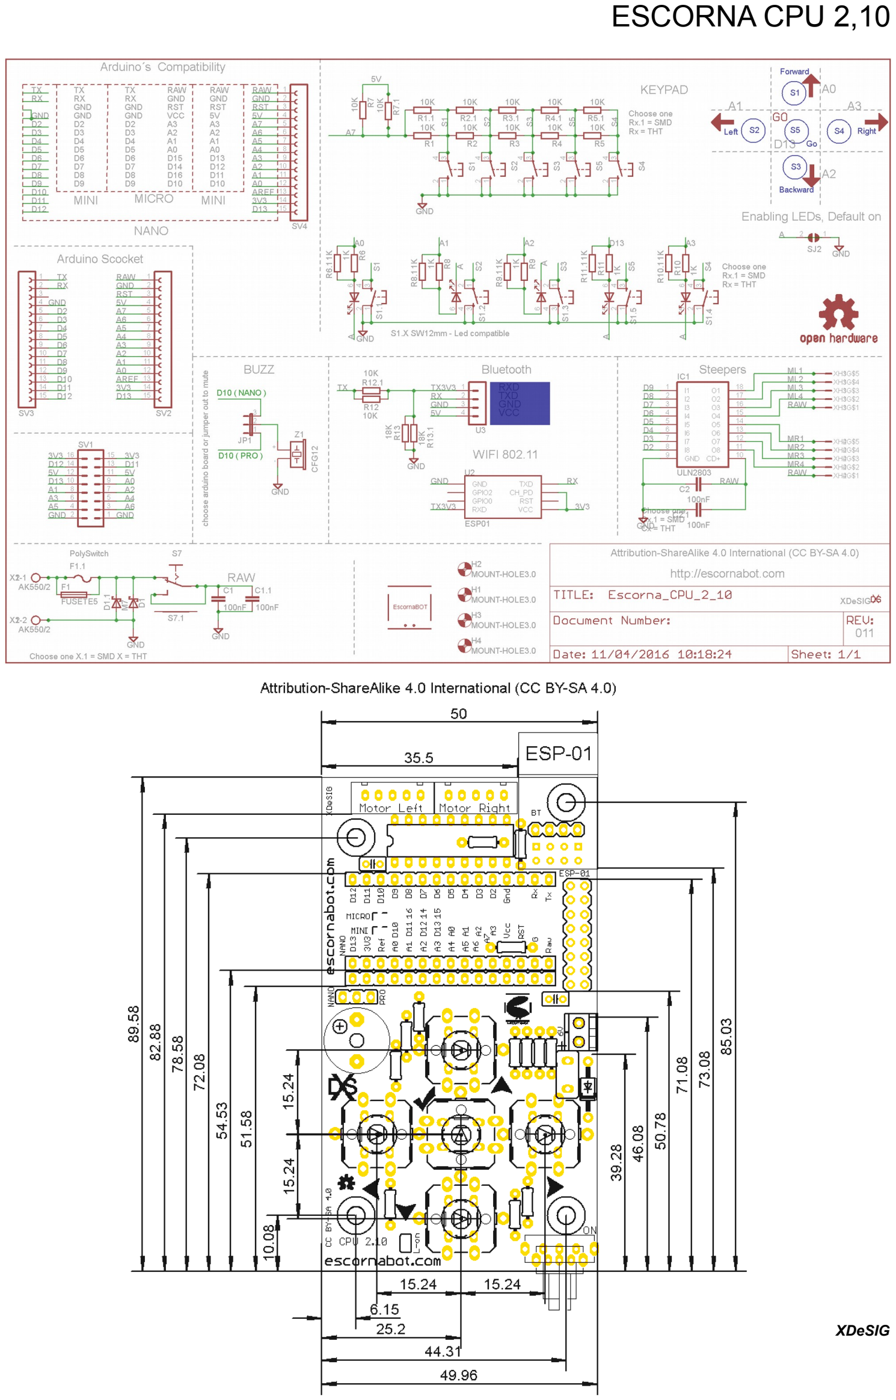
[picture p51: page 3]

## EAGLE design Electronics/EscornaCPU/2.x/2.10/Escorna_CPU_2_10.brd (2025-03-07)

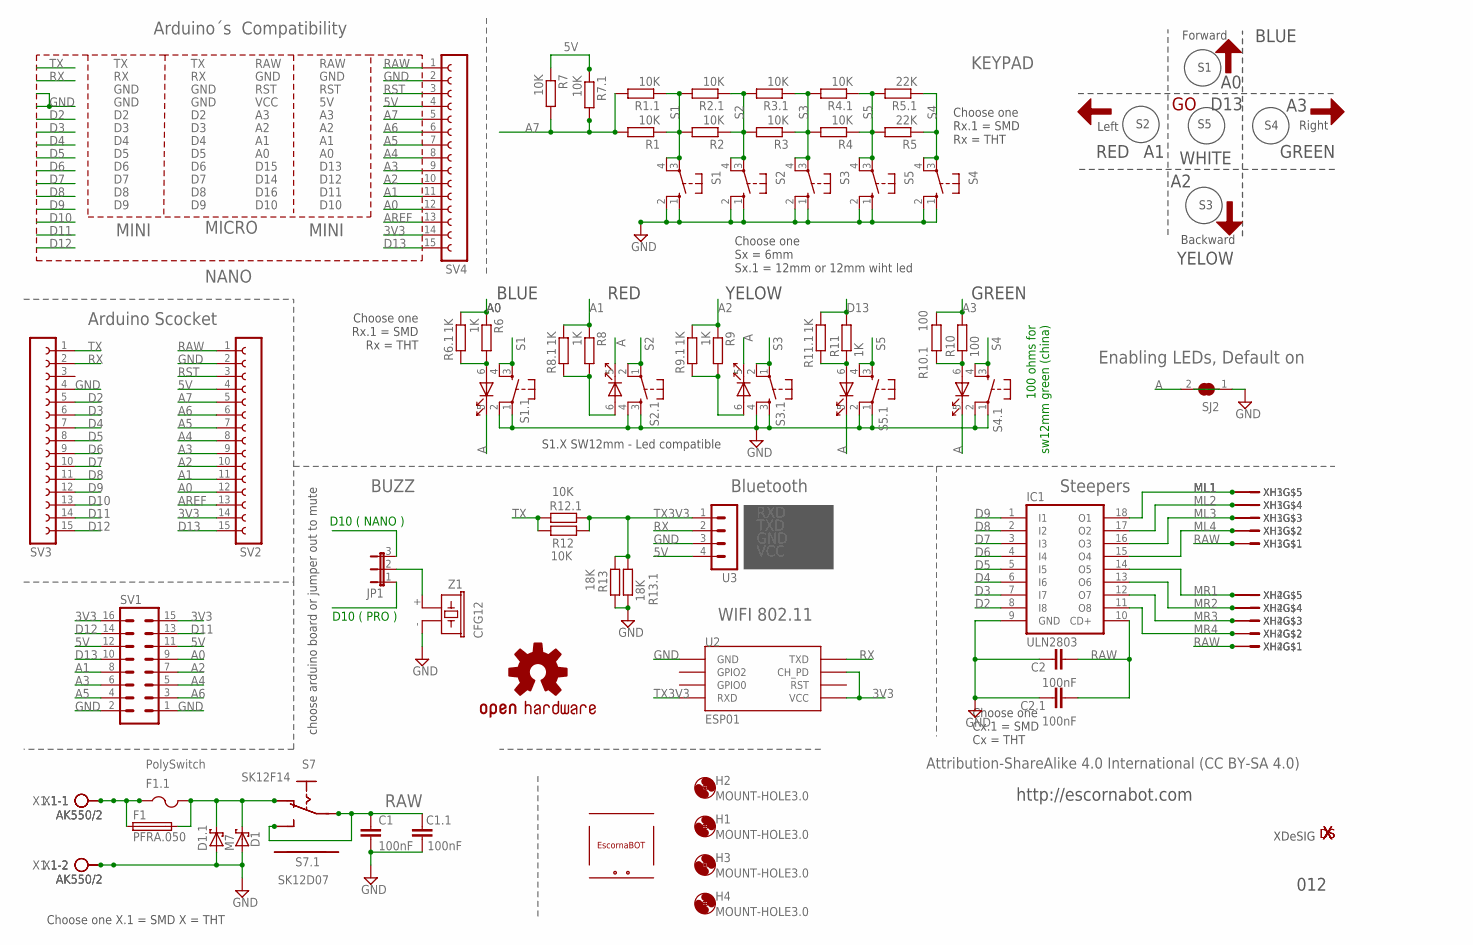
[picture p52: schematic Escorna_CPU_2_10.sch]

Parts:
C1, C2: 100nF; C025-025X050
C1.1, C2.1: 100nF; C1206
D1: 1N5817; DO41-10
D1.1: M7; SMA
ESC: ESCORNABOT; ESCORNA_PEQUE
F1: PFRA.050; TE5
F1.1: PolySwitch; R1206
H1, H2, H3, H4: MOUNT-HOLE3.0; 3,0
IC1: ULN2803; DIL18
JP1: JUMPER_JP2E; JUMPER_JP2
LOGO2: OSHW-LOGOS; OSHW-LOGO-S
R1, R2, R3, R4, R7, R12: 10K; 0204/7
R1.1, R2.1, R3.1, R4.1, R7.1, R12.1: 10K; R0603
R5: 22K; 0204/7
R5.1: 22K; R0603
R6, R8, R9, R11: 1K; 0204/7
R6.1, R8.1, R9.1, R11.1: 1K; R0603
R10: 100; 0204/7
R10.1: 100; R0603
R13: 18K; 0204/7
R13.1: 18K; R0603
S1, S2, S3, S4, S5: 10-XX; B3F-10XX
S1.1, S2.1, S3.1, S4.1, S5.1: B3F-9XXX
S7: SK12F14; ESCORNA_SK-12F14-G
S7.1: SK12D07; ESCORNA_SK-12D07
SJ2: SJ
SV1: MA08-2
SV2, SV3, SV4: CON-LSTA_FE15-1; CON-LSTA_FE15
U2: ESP01
U3: MA04-1
U$1, U$3, U$6, U$11: FRECHA
U$2: GO; VALE
U$13: XDESIG_XDESIG21; XDESIG_XDESIG
X1, X1.1: AK550/2
XDS1: XDESIG; XDESIG_CU_2
XH1, XH2, XH3, XH4: B5B-XH-A
Z1: CFG12; F/CM12P

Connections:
3V3: SV1.15, SV1.16, SV2.14, SV4.14, U2.CH_PD, U2.VCC
5V: R7.1, R7.1.1, SV1.11, SV1.12, SV2.4, SV4.4, U3.4
A: S1.1.5 (K), S2.1.5 (K), S3.1.5 (K), S4.1.5 (K), S5.1.5 (K), SJ2.2
A0: JP1.1, R6.1, R6.1.1, SV1.9, SV2.12, SV4.12
A1: R8.1, R8.1.1, SV1.8, SV2.11, SV4.11
A2: R9.1, R9.1.1, SV1.7, SV2.10, SV4.10
A3: R10.2, R10.1.1, SV1.6, SV2.9, SV4.9
A4: SV1.5, SV2.8, SV4.8
A5: SV1.4, SV2.7, SV4.7
A6: SV1.3, SV2.6, SV4.6
A7: R1.2, R1.1.2, R7.2, R7.1.2, SV2.5, SV4.5
AREF: SV2.13, SV4.13
D2: IC1.8 (I8), SV3.5
D3: IC1.7 (I7), SV3.6
D4: IC1.6 (I6), SV3.7
D5: IC1.5 (I5), SV3.8
D6: IC1.4 (I4), SV3.9
D7: IC1.3 (I3), SV3.10
D8: IC1.2 (I2), SV3.11
D9: IC1.1 (I1), SV3.12
D10: JP1.3, SV3.13
D11: SV1.13, SV3.14
D12: SV1.14, SV3.15
D13: R11.2, R11.1.1, SV1.10, SV2.15, SV4.15
GND: C1.2, C1.1.1, C2.1, C2.1.1, D1.A, D1.1.A, IC1.9 (GND), R13.2, R13.1.1, S1.1 (S), S1.2 (S1), S1.1.1, S1.1.2 (P1), S2.1 (S), S2.2 (S1), S2.1.3 (S), S2.1.4 (S1), S3.1 (S), S3.2 (S1), S3.1.3 (S), S3.1.4 (S1), S4.1 (S), S4.2 (S1), S4.1.1, S4.1.2 (P1), S5.1 (S), S5.2 (S1), S5.1.1, S5.1.2 (P1), SJ2.1, SV1.1, SV1.2, SV2.2, SV3.4, SV4.2, U2.GND, U3.3, X1.2, X1.1.2, Z1.- (2)
ML1: IC1.18 (O1), XH1.P$5, XH3.P$5
ML2: IC1.17 (O2), XH1.P$4, XH3.P$4
ML3: IC1.16 (O3), XH1.P$3, XH3.P$3
ML4: IC1.15 (O4), XH1.P$2, XH3.P$2
MR1: IC1.14 (O5), XH2.P$5, XH4.P$5
MR2: IC1.13 (O6), XH2.P$4, XH4.P$4
MR3: IC1.12 (O7), XH2.P$3, XH4.P$3
MR4: IC1.11 (O8), XH2.P$2, XH4.P$2
unnamed: JP1.2, Z1.+ (1)
unnamed: D1.C, D1.1.C, F1.2, F1.1.2, S7.P$2 (O), S7.1.P$2 (O)
unnamed: R8.2, R8.1.2, S2.1.6 (A)
unnamed: R6.2, R6.1.2, S1.1.6 (A)
unnamed: R9.2, R9.1.2, S3.1.6 (A)
unnamed: R10.1, R10.1.2, S4.1.6 (A)
unnamed: S7.P$4, S7.1.P$4
unnamed: S7.P$5, S7.1.P$5
unnamed: F1.1, F1.1.1, X1.1, X1.1.1
unnamed: R11.1, R11.1.2, S5.1.6 (A)
RAW: C1.1, C1.1.2, C2.2, C2.1.2, IC1.10 (CD+), S7.P$1, S7.P$3 (S), S7.1.P$1, S7.1.P$3 (S), SV2.1, SV4.1, XH1.P$1, XH2.P$1, XH3.P$1, XH4.P$1
RST: SV2.3, SV4.3
RX: SV3.2, U2.TX (TXD), U3.2
S1: R1.1, R1.1.1, R2.2, R2.1.2, S1.3, S1.4 (P1), S1.1.3 (S), S1.1.4 (S1)
S2: R2.1, R2.1.1, R3.2, R3.1.2, S2.3, S2.4 (P1), S2.1.1, S2.1.2 (P1)
S3: R3.1, R3.1.1, R4.2, R4.1.2, S3.3, S3.4 (P1), S3.1.1, S3.1.2 (P1)
S4: R5.1, R5.1.1, S4.3, S4.4 (P1), S4.1.3 (S), S4.1.4 (S1)
S5: R4.1, R4.1.1, R5.2, R5.1.2, S5.3, S5.4 (P1), S5.1.3 (S), S5.1.4 (S1)
TX: R12.1, R12.1.1, SV3.1
TX3V3: R12.2, R12.1.2, R13.1, R13.1.2, U2.RX (RXD), U3.1

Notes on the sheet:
Arduino Scocket
Steepers
KEYPAD
BUZZ
Bluetooth
RXD
TXD
GND
VCC
D10 ( NANO )
D10 ( PRO )
NANO
Arduino´s Compatibility
MINI
MICRO
RAW
RST
D13
D15
D12
D14
D11
D16
D10
Attribution-ShareAlike 4.0 International (CC BY-SA 4.0)
Forward
Left
Right
Backward
WIFI 802.11
Choose one Rx.1 = SMD Rx = THT
Choose one X.1 = SMD X = THT
XDeSIG
http://escornabot.com
Choose one Cx.1 = SMD Cx = THT
S1.X SW12mm - Led compatible
012
Enabling LEDs, Default on
choose arduino board or jumper out to mute
100 ohms for sw12mm green (china)

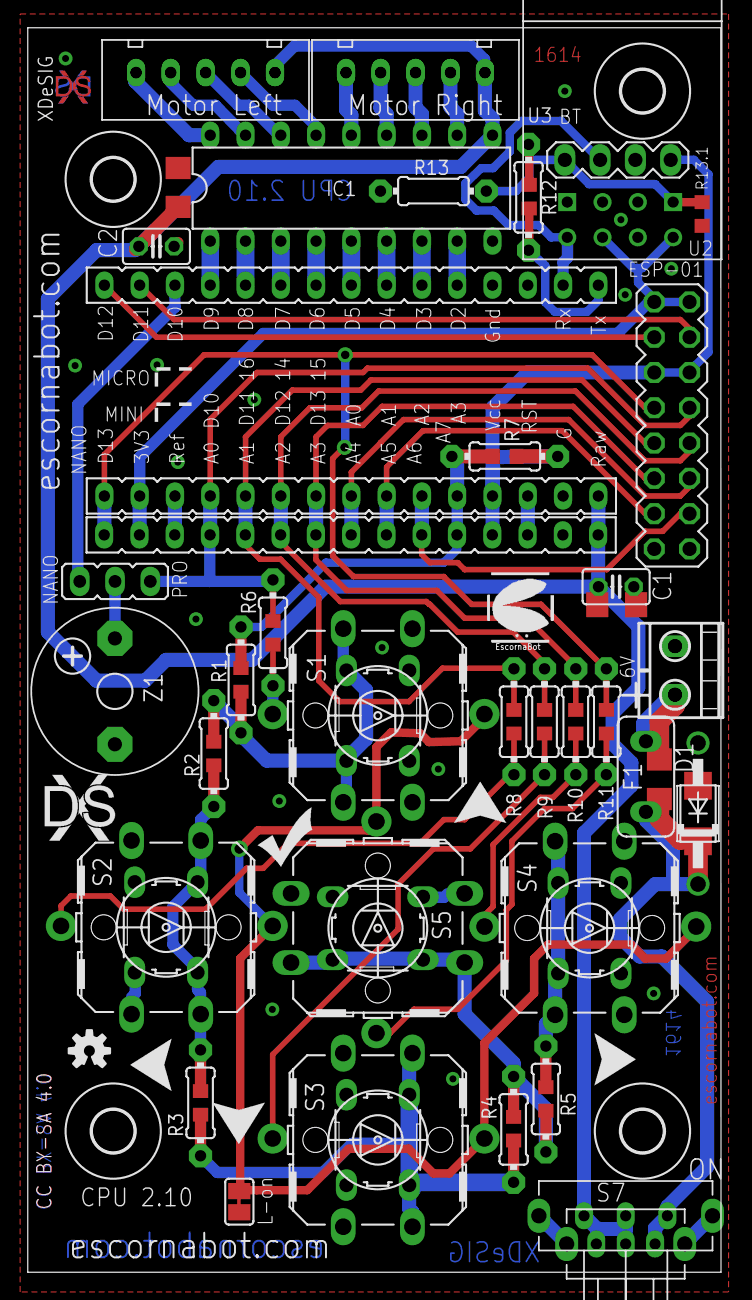
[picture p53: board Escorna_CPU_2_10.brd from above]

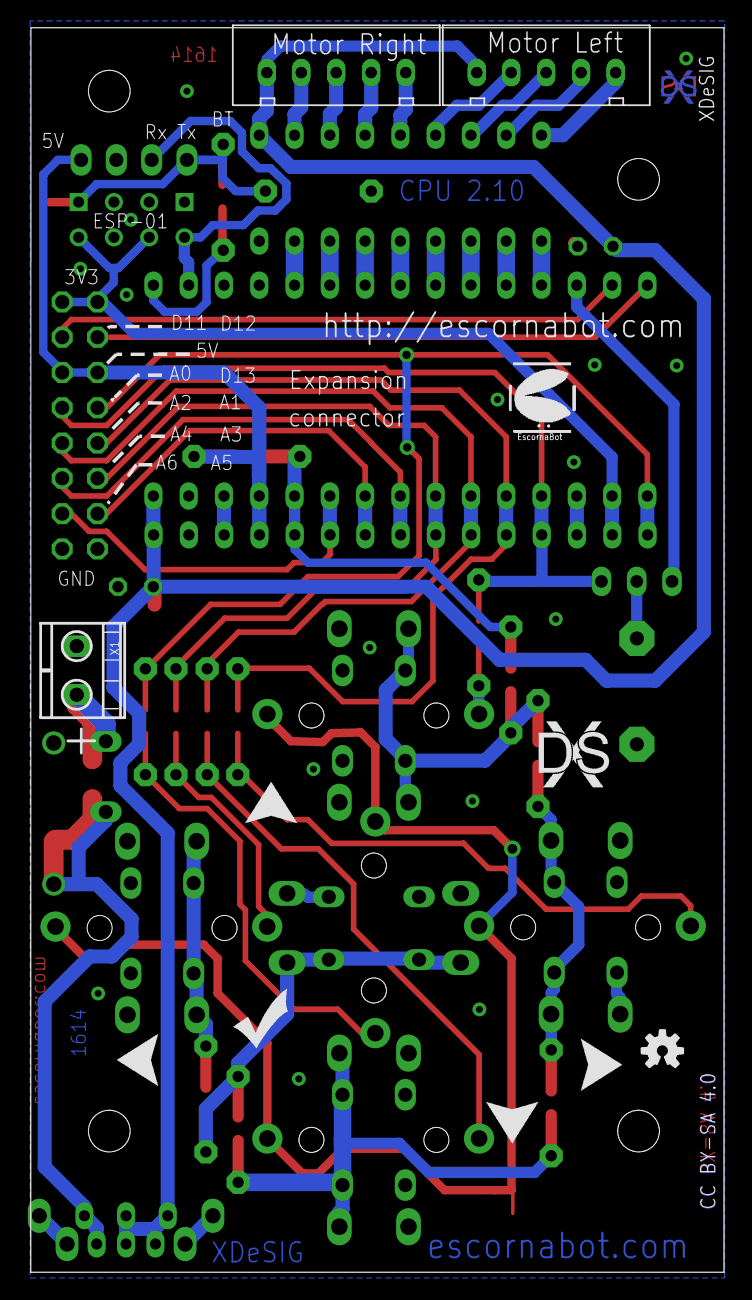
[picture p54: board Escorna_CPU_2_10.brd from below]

Board: 2 copper layers, 49.9 x 89.6 mm, 84 parts (12 on the bottom side), 53 nets.

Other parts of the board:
LOGO1: OSHW-LOGOS; OSHW-LOGO-S
U$4, U$7, U$8, U$9: FRECHA
U$5: ESCORNABOT; ESCORNA_PEQUE
U$10: GO; VALE
U$12: XDESIG_XDESIG21; XDESIG_XDESIG
XDS: XDESIG; XDESIG_CU_2

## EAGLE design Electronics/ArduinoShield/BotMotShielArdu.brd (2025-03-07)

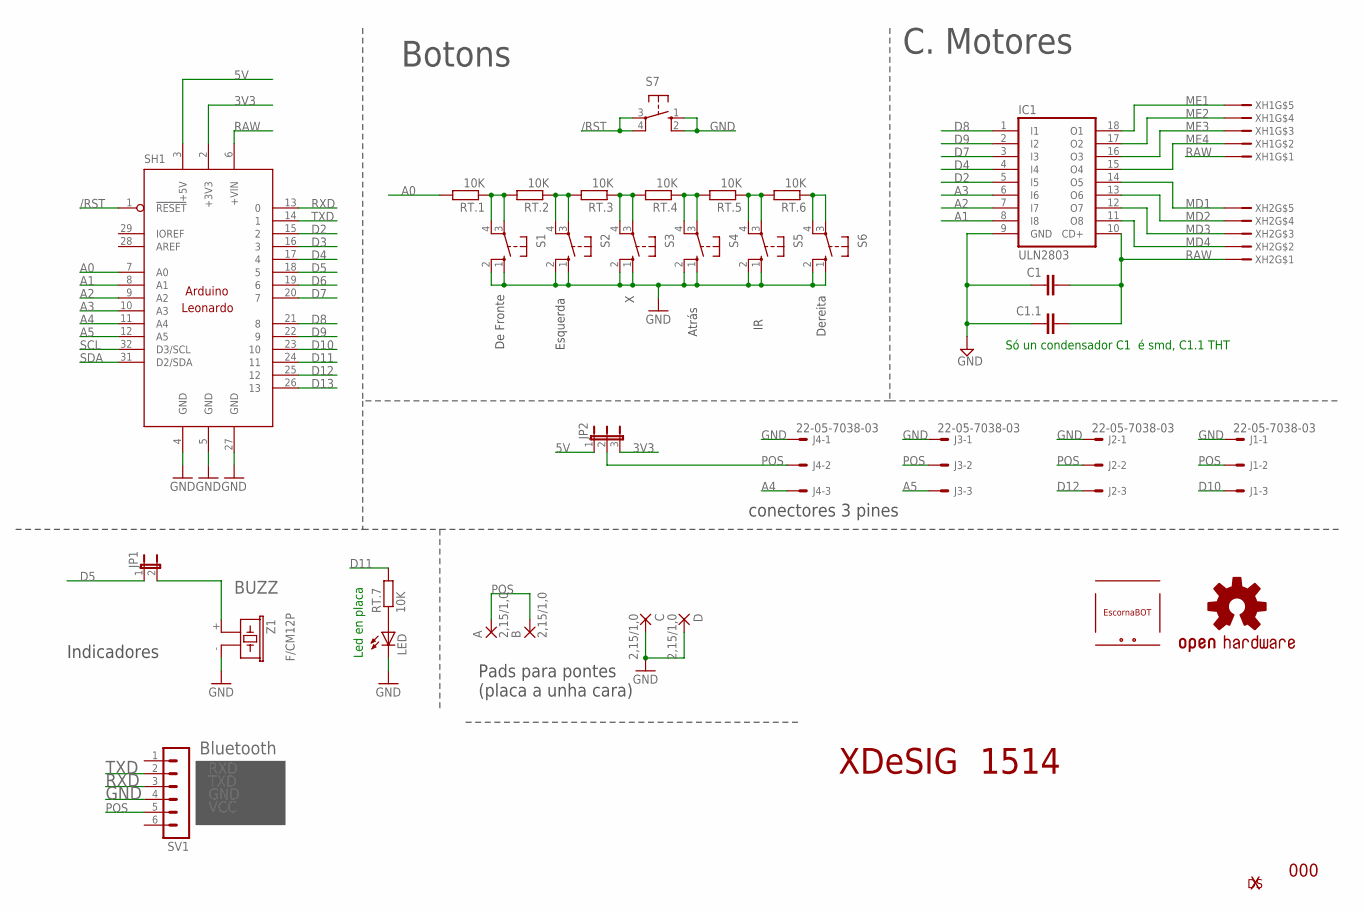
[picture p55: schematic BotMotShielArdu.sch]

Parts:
A: 2,15/1,0
B: 2,15/1,0
C: 2,15/1,0
C1: C-EUC1206; C1206
C1.1: C-EU025-024X044; C025-024X044
D: 2,15/1,0
IC1: ULN2803; DIL18
J1, J2, J3, J4: 22-05-7038-03; 7395-03
JP1: JP1E; JP1
JP2: JP2E; JP2
LED: LED5MM
LOGO4: OSHW-LOGOS; OSHW-LOGO-S
RT.1, RT.2, RT.3, RT.4, RT.5, RT.6, RT.7: 10K; 0204/7
S1, S2, S3, S4, S5, S6: B3F-40XX; B3F40XX_NH
S7: 10-XX; B3F-10XX
SH1: ARDUINO_LEONARDO; LEONARDO
SV1: MA06-1
U$1: ESCORNABOT; ESCORNA_PEQUE
U$3: XDESIG1; XDESIG_CU
XH1, XH2: B5B-XH-A
Z1: F/CM12P

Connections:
3V3: JP2.3, SH1.2 (+3V3)
5V: JP2.1, SH1.3 (+5V)
/RST: S7.3, S7.4 (P1), SH1.1 (!RESET)
A0: RT.1.2, SH1.7 (A0)
A1: IC1.8 (I8), SH1.8 (A1)
A2: IC1.7 (I7), SH1.9 (A2)
A3: IC1.6 (I6), SH1.10 (A3)
A4: J4.3, SH1.11 (A4)
A5: J3.3, SH1.12 (A5)
D2: IC1.5 (I5), SH1.15 (2)
D3: SH1.16 (3)
D4: IC1.4 (I4), SH1.17 (4)
D5: JP1.1, SH1.18 (5)
D6: SH1.19 (6)
D7: IC1.3 (I3), SH1.20 (7)
D8: IC1.1 (I1), SH1.21 (8)
D9: IC1.2 (I2), SH1.22 (9)
D10: J1.3, SH1.23 (10)
D11: RT.7.2, SH1.24 (11)
D12: J2.3, SH1.25 (12)
D13: SH1.26 (13)
GND: C.1, C1.1, C1.1.1, D.1, IC1.9 (GND), J1.1, J2.1, J3.1, J4.1, LED.K (C), S1.1 (S), S1.2 (S1), S2.1 (S), S2.2 (S1), S3.1 (S), S3.2 (S1), S4.1 (S), S4.2 (S1), S5.1 (S), S5.2 (S1), S6.1 (S), S6.2 (S1), S7.1 (S), S7.2 (S1), SH1.4 (GND), SH1.5 (GND), SH1.27 (GND), SV1.4, Z1.- (2)
MD1: IC1.14 (O5), XH2.P$5
MD2: IC1.13 (O6), XH2.P$4
MD3: IC1.12 (O7), XH2.P$3
MD4: IC1.11 (O8), XH2.P$2
ME1: IC1.18 (O1), XH1.P$5
ME2: IC1.17 (O2), XH1.P$4
ME3: IC1.16 (O3), XH1.P$3
ME4: IC1.15 (O4), XH1.P$2
unnamed: LED.A, RT.7.1
unnamed: RT.6.1, S6.3, S6.4 (P1)
unnamed: RT.1.1, RT.2.2, S1.3, S1.4 (P1)
unnamed: JP1.2, Z1.+ (1)
unnamed: RT.5.1, RT.6.2, S5.3, S5.4 (P1)
unnamed: RT.4.1, RT.5.2, S4.3, S4.4 (P1)
unnamed: RT.3.1, RT.4.2, S3.3, S3.4 (P1)
unnamed: RT.2.1, RT.3.2, S2.3, S2.4 (P1)
POS: A.1, B.1, J1.2, J2.2, J3.2, J4.2, JP2.2, SV1.5
RAW: C1.2, C1.1.2, IC1.10 (CD+), SH1.6 (+VIN), XH1.P$1, XH2.P$1
RXD: SH1.13 (0), SV1.3
SCL: SH1.32 (D3/SCL)
SDA: SH1.31 (D2/SDA)
TXD: SH1.14 (1), SV1.2

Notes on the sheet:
Só un condensador C1 é smd, C1.1 THT
De Fronte
Esquerda
Dereita
Atrás
Led en placa
BUZZ
Bluetooth
RXD
TXD
GND
VCC
Botons
C. Motores
conectores 3 pines
Indicadores
Pads para pontes (placa a unha cara)
XDeSIG
1514
000

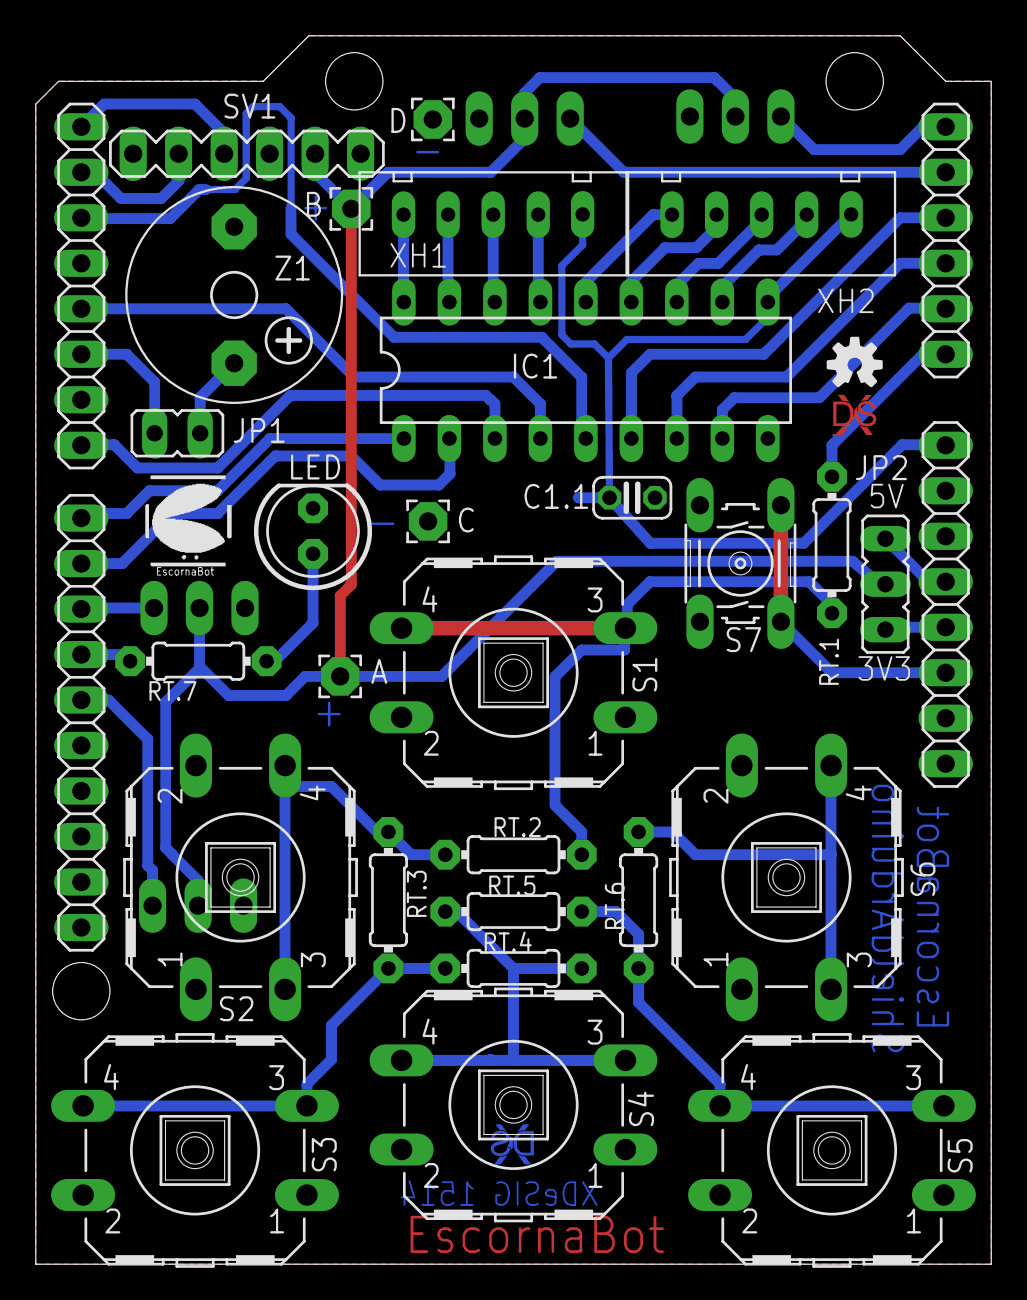
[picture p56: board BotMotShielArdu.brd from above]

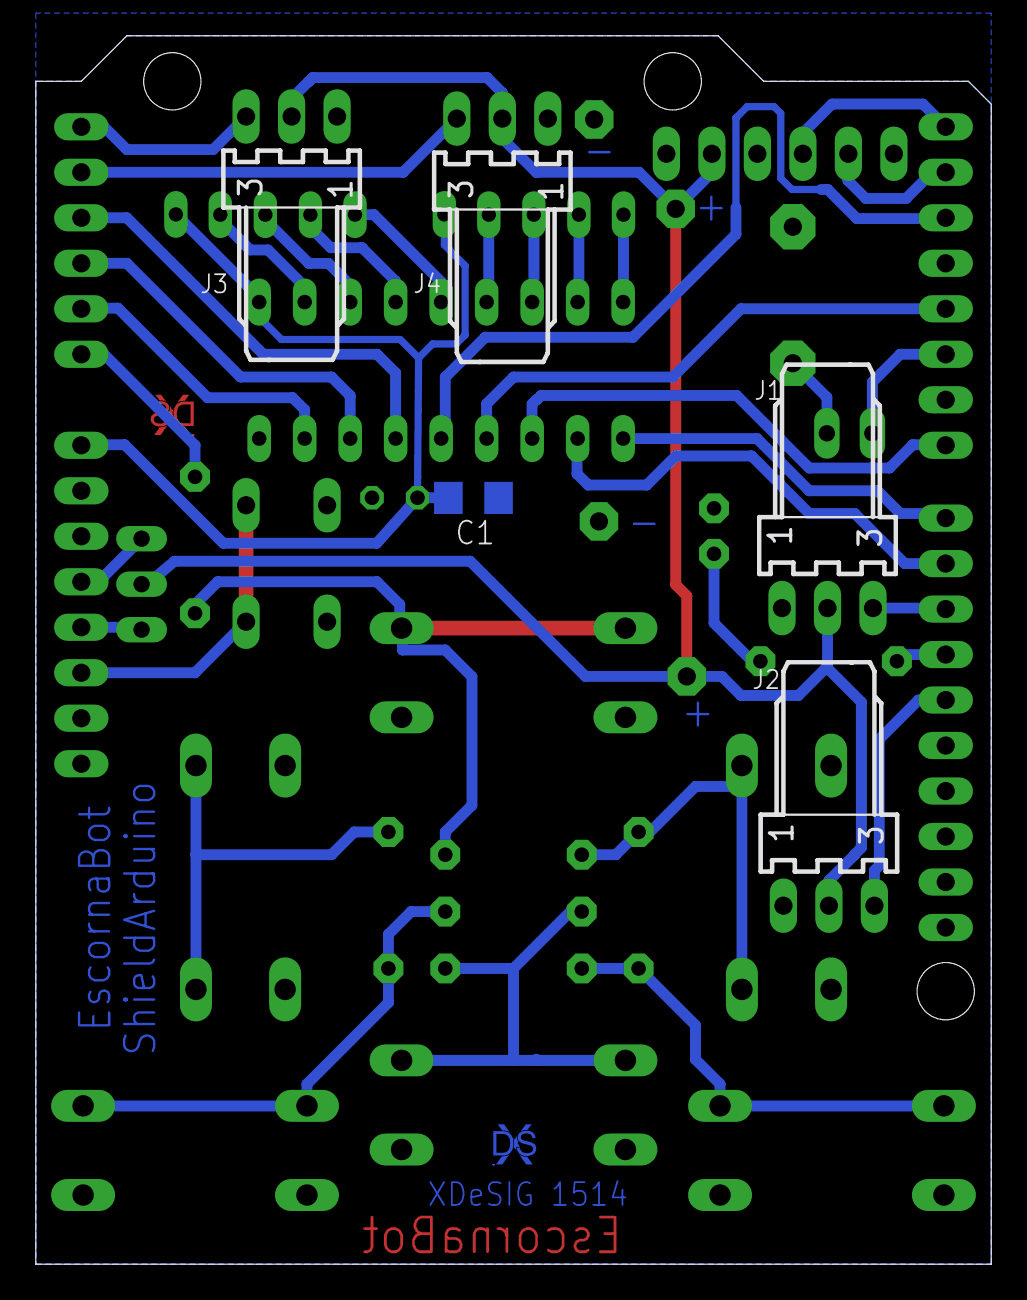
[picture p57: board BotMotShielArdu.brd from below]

Board: 2 copper layers, 53.3 x 68.6 mm, 37 parts (6 on the bottom side), 39 nets.

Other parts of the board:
U$2: XDESIG1; XDESIG_CU

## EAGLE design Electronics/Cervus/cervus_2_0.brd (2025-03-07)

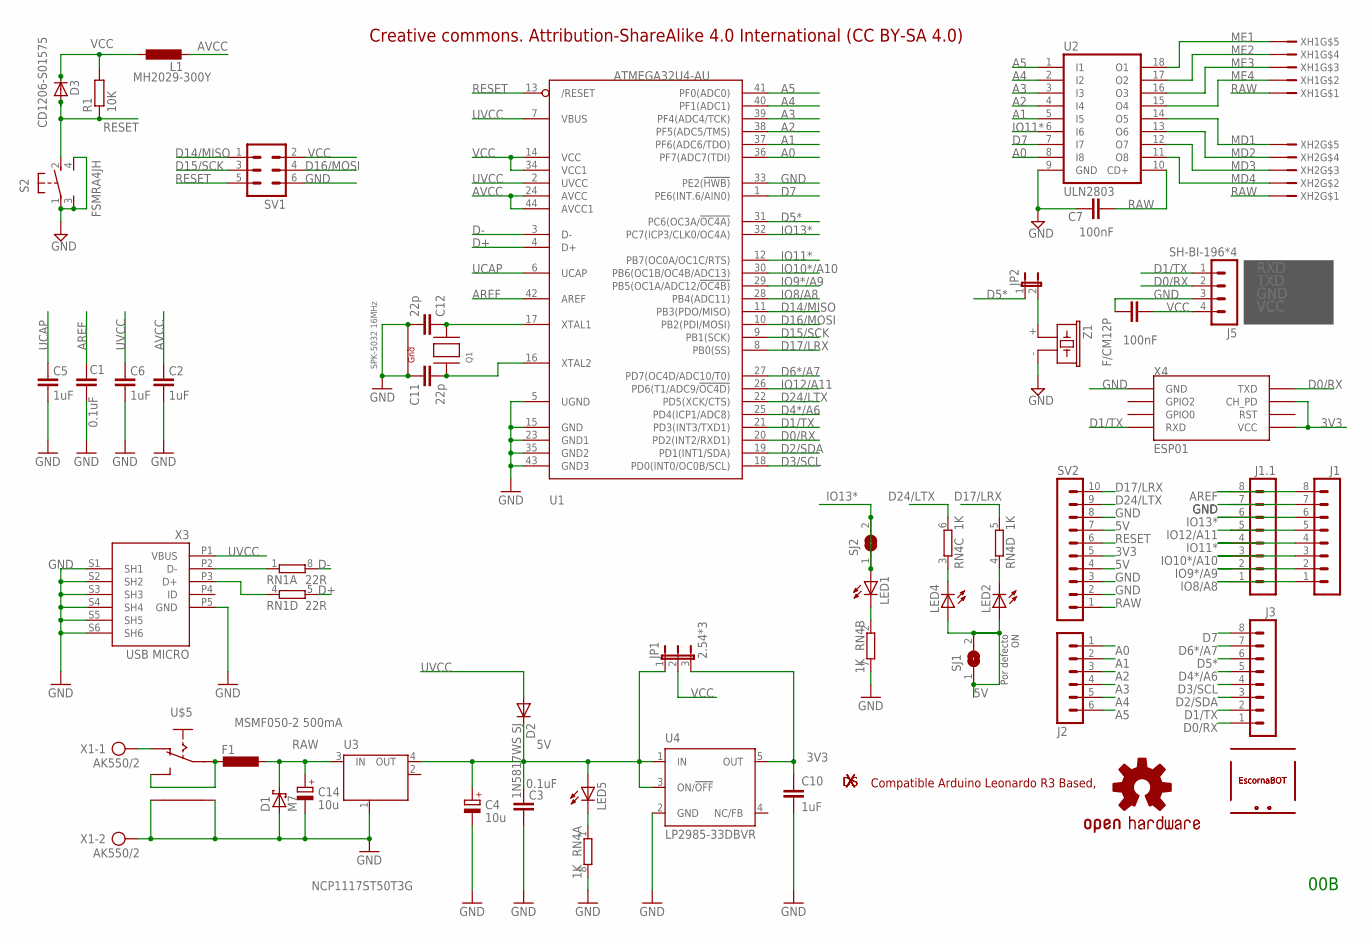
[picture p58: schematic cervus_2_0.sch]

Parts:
C1, C3: 0.1uF; 0603-CAP
C2, C5, C6, C10: 1uF; 0603-CAP
C4, C14: 10u; SMC_B
C7, C8: 100nF; C0603K
C11, C12: 22p; C0603-ROUND
D1: M7; SMA
D2: 1N5817WS SJ; SOD-323
D3: CD1206-S01575; MINIMELF
F1: MSMF050-2 500mA; L1812
J1, J1.1, J3: MA08-1
J2: MA06-1
J5: SH-BI-196*4; MA04-1
JP1: 2.54*3; JP2
JP2: JP1E; JP1
L1: MH2029-300Y; R0805
LED1, LED2, LED4, LED5: LEDCHIPLED_0603; CHIPLED_0603
LOGO1: OSHW-LOGOS; OSHW-LOGO-S
Q1: SPK-5032 16MHz; NX3225
R1: 10K; R0603
RN1: 22R; CAY16
RN4: 1K; CAY16
S2: FSMRA4JH; B3F-31XX
SJ1, SJ2: SJ
SV1: MA03-2
SV2: MA10-1
U1: ATMEGA32U4-AU; TQFP44
U2: ULN2803; DIL18
U3: NCP1117ST50T3G; SOT223
U4: LP2985-33DBVR; SOT23-DBV
U$1, U$2: XDESIG; XDESIG_CU_2
U$3, U$4: ESCORNABOT; ESCORNA_PEQUE
U$5: ESCORNA_SK12F14D; ESCORNA_SK-12D07
X1: AK550/2
X3: USB MICRO; CON2_USB_MICRO_B_AT
X4: ESP01
XH1, XH2: XH2.54-5P; B5B-XH-A
Z1: F/CM12P

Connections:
3V3: C10.1, JP1.3, SV2.5, U4.5 (OUT), X4.CH_PD, X4.VCC
5V: C3.2, C4.+, D2.1 (C), JP1.1, LED2.A, LED4.A, LED5.A, SJ1.1, SJ1.2, SV2.4, SV2.7, U3.4 (OUT), U4.1 (IN), U4.3 (ON/!OFF)
A0: J2.1, U1.36 (PF7(ADC7(TDI)), U2.8 (I8)
A1: J2.2, U1.37 (PF6(ADC6/TDO)), U2.5 (I5)
A2: J2.3, U1.38 (PF5(ADC5/TMS)), U2.4 (I4)
A3: J2.4, U1.39 (PF4(ADC4/TCK)), U2.3 (I3)
A4: J2.5, U1.40 (PF1(ADC1)), U2.2 (I2)
A5: J2.6, U1.41 (PF0(ADC0)), U2.1 (I1)
AREF: C1.2, J1.8, J1.1.8, U1.42 (AREF)
AVCC: C2.2, L1.2, U1.24 (AVCC), U1.44 (AVCC1)
D0/RX: J3.1, J5.2, U1.20 (PD2(INT2/RXD1)), X4.TX (TXD)
D1/TX: J3.2, J5.1, U1.21 (PD3(INT3/TXD1)), X4.RX (RXD)
D2/SDA: J3.3, U1.19 (PD1(INT1/SDA))
D3/SCL: J3.4, U1.18 (PD0(INT0/OC0B/SCL))
D4*/A6: J3.5, U1.25 (PD4(ICP1/ADC8))
D5*: J3.6, JP2.1, U1.31 (PC6(OC3A/!OC4A))
D6*/A7: J3.7, U1.27 (PD7(OC4D/ADC10/T0))
D7: J3.8, U1.1 (PE6(INT.6/AIN0)), U2.7 (I7)
D14/MISO: SV1.1, U1.11 (PB3(PDO/MISO))
D15/SCK: SV1.3, U1.9 (PB1(SCK))
D16/MOSI: SV1.4, U1.10 (PB2(PDI/MOSI))
D17/LRX: RN4.5 (2), SV2.10, U1.8 (PB0(SS))
D24/LTX: RN4.6 (2), SV2.9, U1.22 (PD5(XCK/CTS))
D+: RN1.5 (2), U1.4 (D+)
D-: RN1.8 (2), U1.3 (D-)
GND: C1.1, C2.1, C3.1, C4.-, C5.1, C6.1, C7.1, C8.1, C10.2, C11.1, C12.2, C14.-, D1.A, J1.7, J1.1.7, J5.3, Q1.2 (G2), Q1.4 (G1), RN4.7 (2), RN4.8 (2), S2.1, S2.3 (CH2), S2.4 (CH1), SV1.6, SV2.2, SV2.3, SV2.8, U1.5 (UGND), U1.15 (GND), U1.23 (GND1), U1.33 (PE2(!HWB)), U1.35 (GND2), U1.43 (GND3), U2.9 (GND), U3.1 (GND/ADJ), U4.2 (GND), U$5.P$4, U$5.P$5, X1.2, X3.P5 (GND), X3.S1 (SH1), X3.S2 (SH2), X3.S3 (SH3), X3.S4 (SH4), X3.S5 (SH5), X3.S6 (SH6), X4.GND, Z1.- (2)
IO8/A8: J1.1, J1.1.1, U1.28 (PB4(ADC11))
IO9*/A9: J1.2, J1.1.2, U1.29 (PB5(OC1A/ADC12/!OC4B))
IO10*/A10: J1.3, J1.1.3, U1.30 (PB6(OC1B/OC4B/ADC13))
IO11*: J1.4, J1.1.4, U1.12 (PB7(OC0A/OC1C/RTS)), U2.6 (I6)
IO12/A11: J1.5, J1.1.5, U1.26 (PD6(T1/ADC9/!OC4D))
IO13*: J1.6, J1.1.6, LED1.A, SJ2.1, SJ2.2, U1.32 (PC7(ICP3/CLK0/OC4A))
MD1: U2.14 (O5), XH2.P$5
MD2: U2.13 (O6), XH2.P$4
MD3: U2.12 (O7), XH2.P$3
MD4: U2.11 (O8), XH2.P$2
ME1: U2.18 (O1), XH1.P$5
ME2: U2.17 (O2), XH1.P$4
ME3: U2.16 (O3), XH1.P$3
ME4: U2.15 (O4), XH1.P$2
unnamed: LED5.C, RN4.1
unnamed: LED1.C, RN4.2 (1)
unnamed: LED4.C, RN4.3 (1)
unnamed: LED2.C, RN4.4 (1)
unnamed: F1.2, U$5.P$1, U$5.P$3 (S)
unnamed: C11.2, Q1.1 (X1), U1.16 (XTAL2)
unnamed: C12.1, Q1.3 (X2), U1.17 (XTAL1)
unnamed: JP2.2, Z1.+ (1)
unnamed: RN1.1, X3.P2 (D-)
unnamed: RN1.4 (1), X3.P3 (D+)
unnamed: U$5.P$2 (O), X1.1
RAW: C7.2, C14.+, D1.C, F1.1, SV2.1, U2.10 (CD+), U3.3 (IN), XH1.P$1, XH2.P$1
RESET: D3.A, R1.1, S2.2 (S), SV1.5, SV2.6, U1.13 (/RESET)
UCAP: C5.2, U1.6 (UCAP)
UVCC: C6.2, D2.2 (A), U1.2 (UVCC), U1.7 (VBUS), X3.P1 (VBUS)
VCC: C8.2, D3.C, J5.4, JP1.2, L1.1, R1.2, SV1.2, U1.14 (VCC), U1.34 (VCC1)

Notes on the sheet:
RXD
TXD
GND
VCC
00B
Por defecto ON
Creative commons. Attribution-ShareAlike 4.0 International (CC BY-SA 4.0)
Compatible Arduino Leonardo R3 Based,

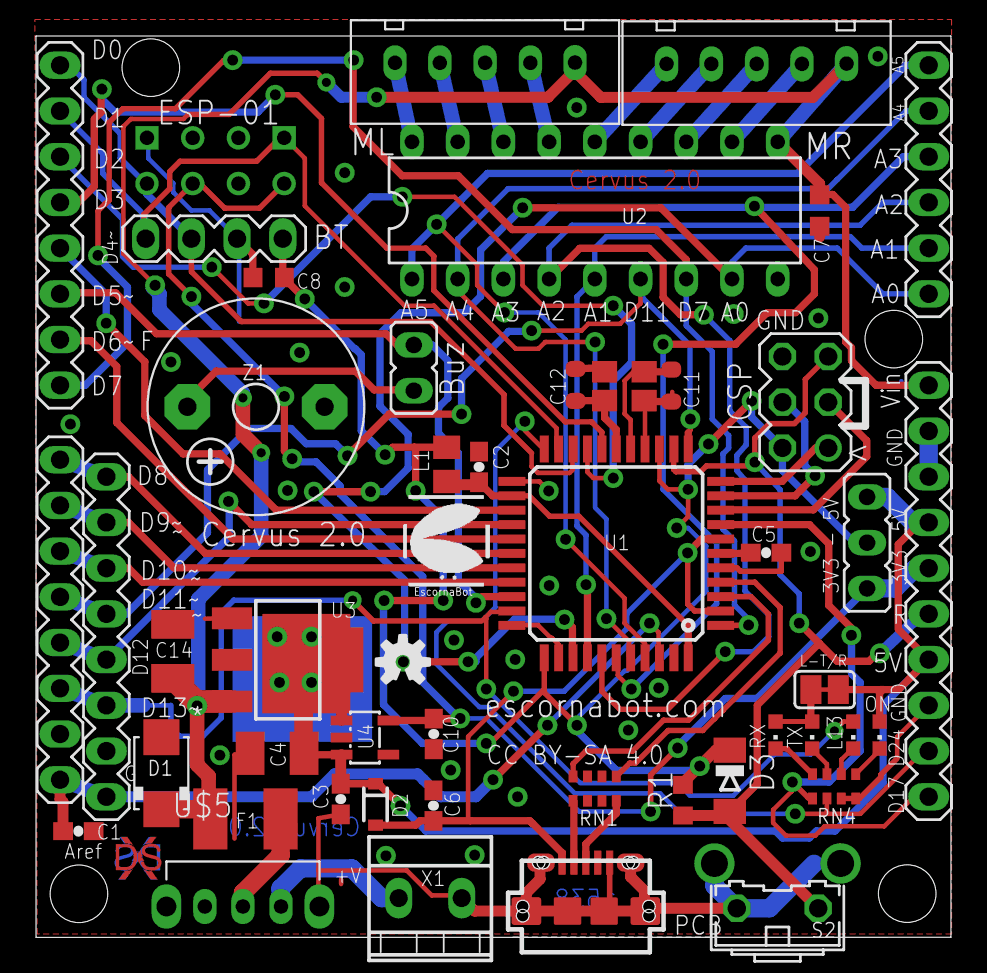
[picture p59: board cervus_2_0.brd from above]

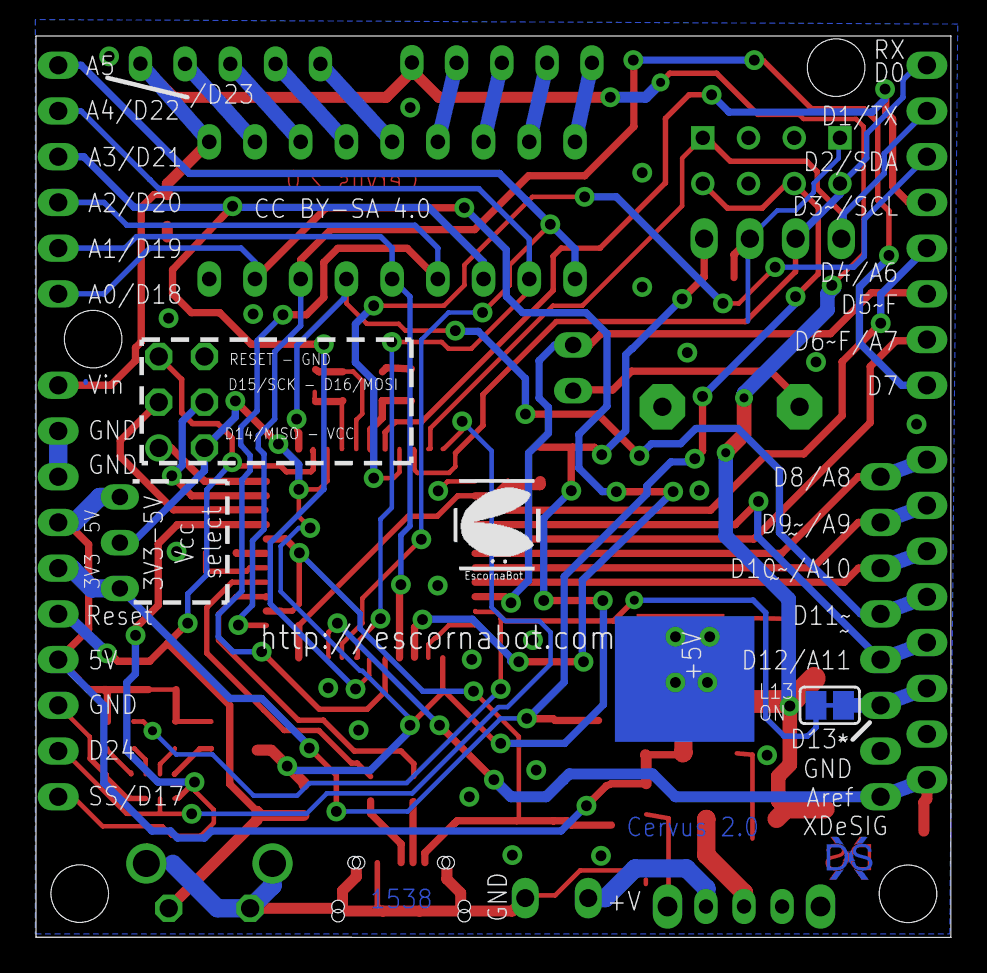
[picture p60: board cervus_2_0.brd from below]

Board: 2 copper layers, 50.8 x 50.1 mm, 53 parts (3 on the bottom side), 56 nets.

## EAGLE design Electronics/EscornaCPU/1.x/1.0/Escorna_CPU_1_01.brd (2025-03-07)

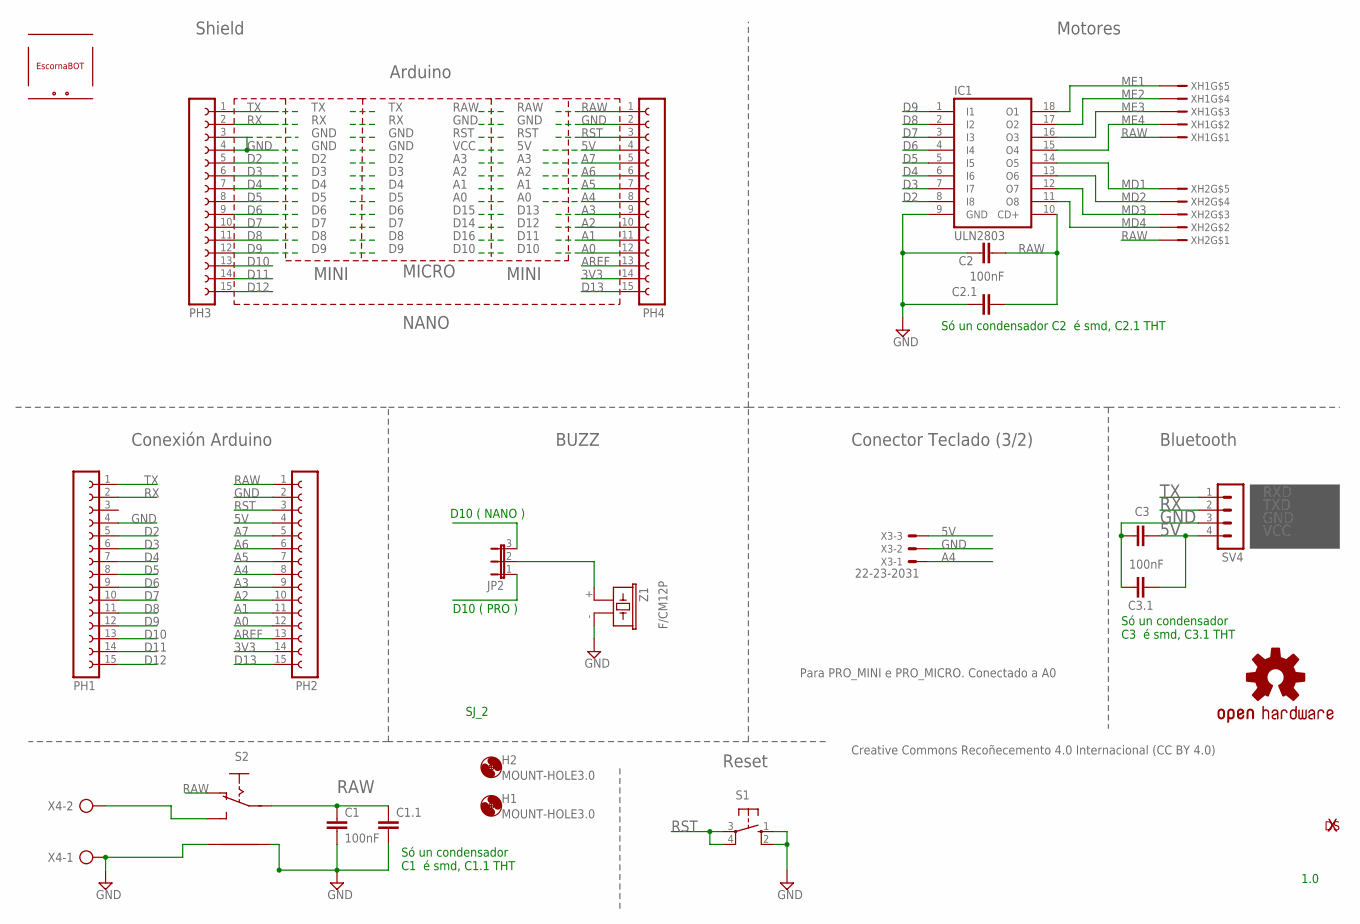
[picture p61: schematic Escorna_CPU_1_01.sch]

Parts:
C1, C2, C3: 100nF; C1206
C1.1, C2.1, C3.1: C-EU025-024X044; C025-024X044
H1, H2: MOUNT-HOLE3.0; 3,0
IC1: ULN2803; DIL18
JP2: JP2E; JP2
LOGO1: OSHW-LOGOS; OSHW-LOGO-S
PH1, PH2, PH3, PH4: FE15-1; FE15
S1: 10-XX; B3F-10XX
S2: SK12F14F; SK-12F14-G
SV4: MA04-1
U$1: ESCORNABOT; ESCORNA_PEQUE
U$6: XDESIG; XDESIG_CU_2
X3: 22-23-2031
X4: AK500/2
XH1, XH2: B5B-XH-A
Z1: F/CM12P

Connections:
3V3: PH2.14, PH4.14
5V: C3.2, C3.1.2, PH2.4, PH4.4, SV4.4, X3.3
A0: JP2.1, PH2.12, PH4.12
A1: PH2.11, PH4.11
A2: PH2.10, PH4.10
A3: PH2.9, PH4.9
A4: PH2.8, PH4.8, X3.1
A5: PH2.7, PH4.7
A6: PH2.6, PH4.6
A7: PH2.5, PH4.5
AREF: PH2.13, PH4.13
D2: IC1.8 (I8), PH1.5, PH3.5
D3: IC1.7 (I7), PH1.6, PH3.6
D4: IC1.6 (I6), PH1.7, PH3.7
D5: IC1.5 (I5), PH1.8, PH3.8
D6: IC1.4 (I4), PH1.9, PH3.9
D7: IC1.3 (I3), PH1.10, PH3.10
D8: IC1.2 (I2), PH1.11, PH3.11
D9: IC1.1 (I1), PH1.12, PH3.12
D10: JP2.3, PH1.13, PH3.13
D11: PH1.14, PH3.14
D12: PH1.15, PH3.15
D13: PH2.15, PH4.15
GND: C1.2, C1.1.2, C2.1, C2.1.1, C3.1, C3.1.1, IC1.9 (GND), PH1.4, PH2.2, PH3.3, PH3.4, PH4.2, S1.1 (S), S1.2 (S1), S2.P$4, S2.P$5, SV4.3, X3.2, X4.1, Z1.- (2)
MD1: IC1.14 (O5), XH2.P$5
MD2: IC1.13 (O6), XH2.P$4
MD3: IC1.12 (O7), XH2.P$3
MD4: IC1.11 (O8), XH2.P$2
ME1: IC1.18 (O1), XH1.P$5
ME2: IC1.17 (O2), XH1.P$4
ME3: IC1.16 (O3), XH1.P$3
ME4: IC1.15 (O4), XH1.P$2
unnamed: JP2.2, Z1.+ (1)
unnamed: S2.P$3 (S), X4.2
RAW: C1.1, C1.1.1, C2.2, C2.1.2, IC1.10 (CD+), PH2.1, PH4.1, S2.P$1, S2.P$2 (O), XH1.P$1, XH2.P$1
RST: PH2.3, PH4.3, S1.3, S1.4 (P1)
RX: PH1.2, PH3.2, SV4.2
TX: PH1.1, PH3.1, SV4.1

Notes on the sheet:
1.0
Conexión Arduino
Motores
Conector Teclado (3/2)
BUZZ
Bluetooth
RXD
TXD
GND
VCC
Reset
Para PRO_MINI e PRO_MICRO. Conectado a A0
D10 ( NANO )
D10 ( PRO )
SJ_2
Só un condensador C2 é smd, C2.1 THT
Só un condensador C3 é smd, C3.1 THT
Só un condensador C1 é smd, C1.1 THT
Shield
NANO
Arduino
MINI
MICRO
RAW
RST
D13
D15
D12
D14
D11
D16
D10
Creative Commons Recoñecemento 4.0 Internacional (CC BY 4.0)

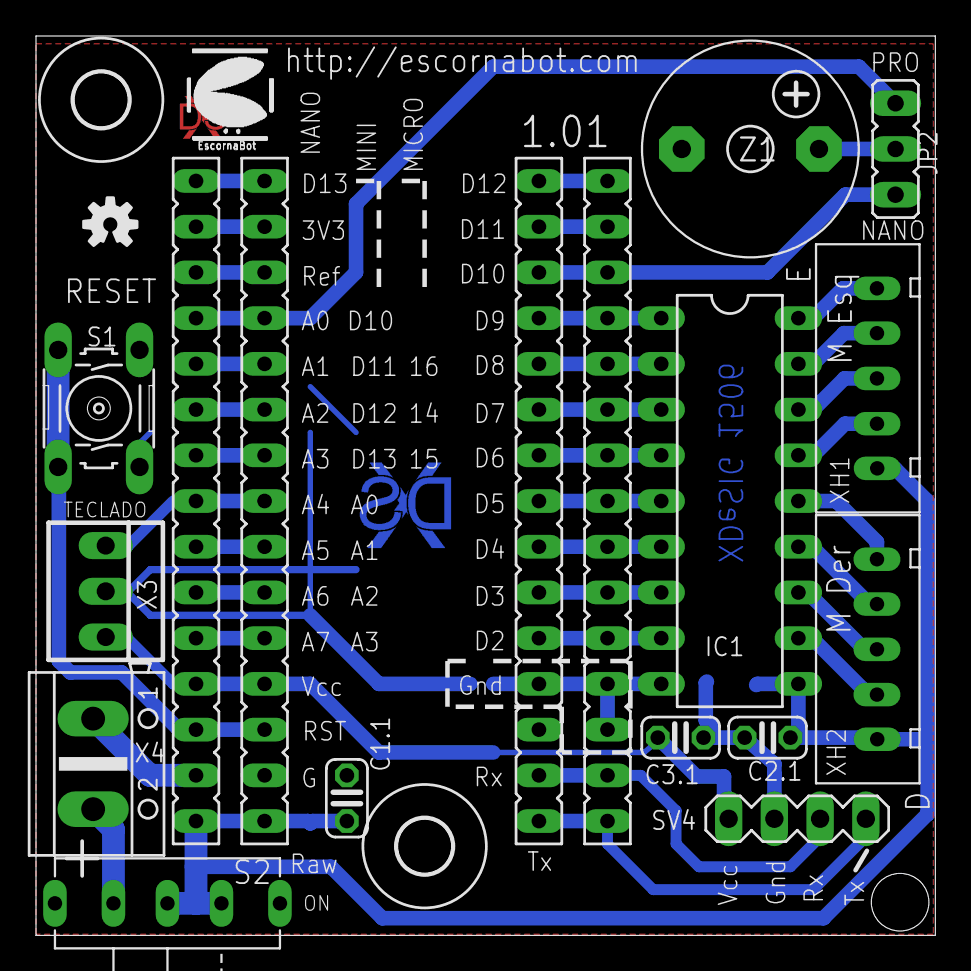
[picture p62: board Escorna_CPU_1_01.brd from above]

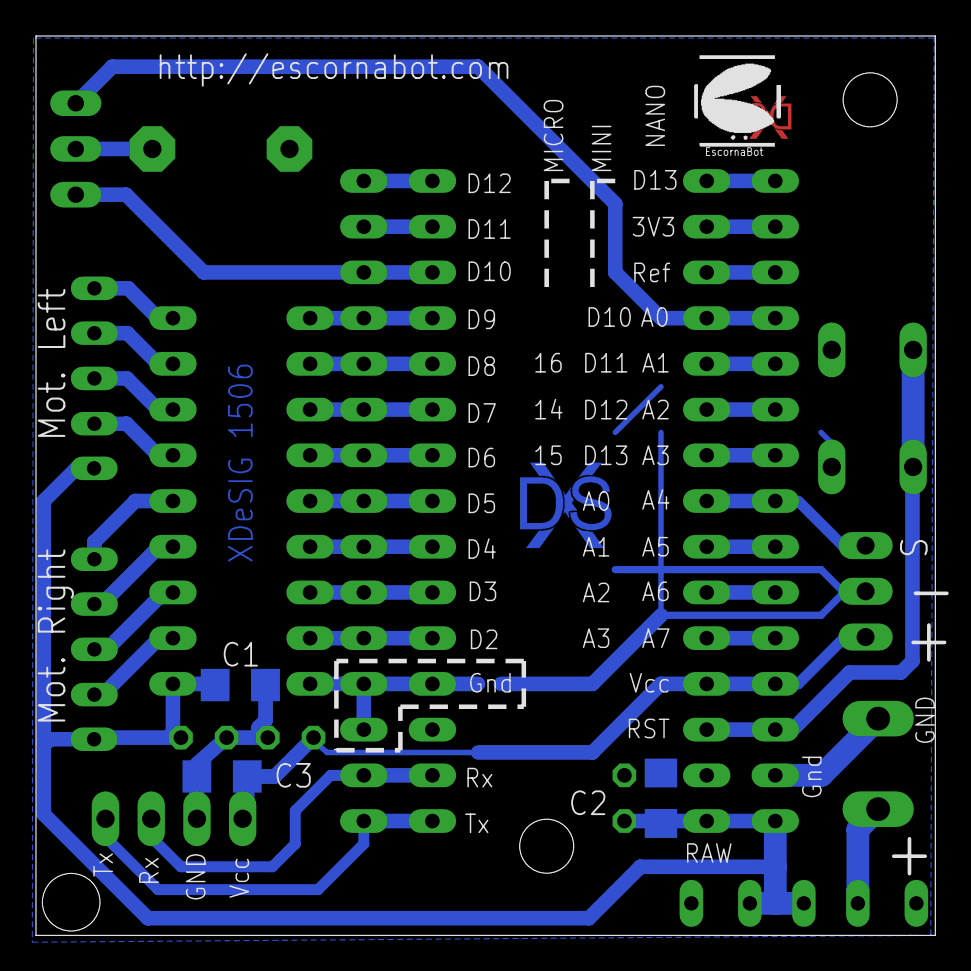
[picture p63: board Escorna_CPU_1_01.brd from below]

Board: 2 copper layers, 50.0 x 50.0 mm, 28 parts (5 on the bottom side), 38 nets.

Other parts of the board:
U$2, U$5: ESCORNABOT; ESCORNA_PEQUE
U$3: XDESIG; XDESIG_CU

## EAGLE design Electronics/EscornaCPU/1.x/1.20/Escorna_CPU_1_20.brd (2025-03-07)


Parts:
C1, C3: 100nF; C025-025X050
C1.1, C3.1: 100nF; C0603K
C2: 1uF; C1206K
D1: 1N5817; DO41-10
D1.1: M7; SMA-DO214AC
ESC1, ESC2: ESCORNABOT; ESCORNA_PEQUE
F1: PFRA.050; TE5
F1.1: PolySwitch; R1206
H3, H4: H3.0; 3,0
IC1: ULN2803; DIL18
JP1, JP2: JP1E; 1X02
JP3, JP4: JP1E; JP1
JP5: JP4E; JP4
LOGO2: OSHW-LOGOS; OSHW-LOGO-S
R1, R2, R4, R5: 10K; 0204/7
R1.1, R2.1, R4.1, R5.1: 10K; R0603
R3: 18K; 0204/7
R3.1: 18K; R0603
S7: SK12F14; ESCORNA_SK-12F14-G
S7.1: SK12D07; ESCORNA_SK-12D07
SJ1: SJ
SV1, SV2: 1x15 SOCKET STRIP; CON-LSTA_FE15
SV3, SV4, SV5, SV6: MA06-1
U2: ESP01
U3: MA04-1
U6: 1117-3.3; SOT223
U$1, U$13: XDESIG_XDESIG21; XDESIG_XDESIG
X1, X1.1: AK550/2
XDS1: XDESIG; XDESIG_CU_2
XH1, XH2, XH3, XH4: B5B-XH-A
Z1: CFG12; F/CM12P

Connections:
3.3V: SJ1.2, SV2.14
3V3: R4.1, R4.1.1, R5.1, R5.1.1, SJ1.1, U2.VCC, U6.4 (VOUTT)
5V: JP3.1, JP3.2, JP5.3, R1.1, R1.1.1, SV2.4, SV4.1, SV4.2, SV4.3, SV4.4, SV4.5, SV4.6, U3.4
A0: SV2.12, SV6.1
A1: SV2.11, SV6.2
A2: SV2.10, SV6.3
A3: SV2.9, SV6.4
A4: JP5.1, SV2.8, SV3.1
A5: JP5.2, SV2.7, SV3.2
A6: SV2.6, SV3.3
A7: R1.2, R1.1.2, SV2.5, SV6.5
AREF: SV2.13
CH: R4.2, R4.1.2, U2.GPIO0
D2: IC1.8 (I8), SV1.5
D3: IC1.7 (I7), SV1.6
D4: IC1.6 (I6), SV1.7
D5: IC1.5 (I5), SV1.8
D6: IC1.4 (I4), SV1.9
D7: IC1.3 (I3), SV1.10
D8: IC1.2 (I2), SV1.11
D9: IC1.1 (I1), SV1.12
D10: JP1.2, SV1.13
D11: SV1.14, SV3.4
D12: SV1.15, SV3.5
D13: SV2.15, SV3.6
GND: C1.2, C1.1.1, C2.1, C3.1, C3.1.1, D1.A, D1.1.A, IC1.9 (GND), JP2.1, JP4.1, JP4.2, JP5.4, R3.2, R3.1.1, SV1.4, SV2.2, SV5.1, SV5.2, SV5.3, SV5.4, SV5.5, SV5.6, SV6.6, U2.GND, U3.3, U6.1 (GAJ), X1.1, X1.1.2, Z1.- (2)
ML1: IC1.18 (O1), XH1.P$5, XH3.P$5
ML2: IC1.17 (O2), XH1.P$4, XH3.P$4
ML3: IC1.16 (O3), XH1.P$3, XH3.P$3
ML4: IC1.15 (O4), XH1.P$2, XH3.P$2
MR1: IC1.14 (O5), XH2.P$5, XH4.P$5
MR2: IC1.13 (O6), XH2.P$4, XH4.P$4
MR3: IC1.12 (O7), XH2.P$3, XH4.P$3
MR4: IC1.11 (O8), XH2.P$2, XH4.P$2
unnamed: R5.2, R5.1.2, U2.CH_PD
unnamed: JP1.1, Z1.+ (1)
unnamed: F1.1, F1.1.1, JP2.2, X1.2, X1.1.1
unnamed: S7.P$4, S7.1.P$4
unnamed: S7.P$5, S7.1.P$5
RAW: C1.1, C1.1.2, C2.2, C3.2, C3.1.2, IC1.10 (CD+), S7.P$2 (O), S7.1.P$2 (O), SV2.1, U6.3 (VIN), XH1.P$1, XH2.P$1, XH3.P$1, XH4.P$1
RST: SV2.3, U2.RST
RX: SV1.2, U2.TX (TXD), U3.2
TX: R2.1, R2.1.1, SV1.1
TX3V3: R2.2, R2.1.2, R3.1, R3.1.2, U2.RX (RXD), U3.1
VIN: D1.C, D1.1.K (C), F1.2, F1.1.2, S7.P$1, S7.P$3 (S), S7.1.P$1, S7.1.P$3 (S)

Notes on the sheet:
Arduino Scocket
Steepers
BUZZ
Bluetooth
Buzz on
NANO
Arduino´s Compatibility
MINI
MICRO
GND
RAW
RST
VCC
D13
D15
D12
D14
D11
D16
D10
Attribution-ShareAlike 4.0 International (CC BY-SA 4.0)
WIFI 802.11
Choose one X.1 = SMD X = THT
XDeSIG
By XDeSIG
Choose one Cx.1 = SMD Cx = THT
000
SCL
SDA
Choose one Rx.1 = SMD Rx = THT
Select 3,3V Arduino Or external
Connector to keypad leds..
to oled I2C...
to Servos, sensors...



Board: 2 copper layers, 50.0 x 50.0 mm, 55 parts (8 on the bottom side), 44 nets.

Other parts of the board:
ESC: ESCORNABOT; ESCORNA_PEQUE
H7: MOUNT-HOLE3.0; 3,0
XDS: XDESIG; XDESIG_CU_2

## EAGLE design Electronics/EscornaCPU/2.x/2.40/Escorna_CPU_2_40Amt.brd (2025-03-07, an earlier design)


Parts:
$1_82_$: XDESIG_XDESIG21; XDESIG_XDESIG
$1_83_$: B5B-XH-A
C1, C4, C5, C8, C10, C11: 100nF; C0603-ROUND
C2, C9: 22uF; C1206K
C3: 10uF; C1206K
C6: 100nF; C025-024X044
C6.1: 100nF; C0603K
C7: 1uF; C0603-ROUND
D1: SS14; SMADIODE
D2: 1N5817; DO41-10
D3: 1PS76SB10.115; SOD-323F
D4: SS34; DIODE_SMA
ESC: ESCORNABOT; ESCORNA_PEQUE
F1: PFRA.050; TE5
F1.1: ERF-RA05060Z; R1206
F3: 0,5; R1206
H1, H2, H3, H4: 3.0; 3,0
IC2: ULN2803; DIL18
IC3: ATMEGA328P-AU; TQFP32-08
IC4: SX1308; SOT23-6
ICSP: 0114_PH254-203DF118A00V; 2X03
J1: 2.54; 6410-02
J2: 10118194-0001LF/C; SMARTPRJ_CON2_USB_MICRO_B_AT
J3, J5: ZL262-4SG; MA04-1
JP1: ZL201-02G; JP1
L1: 4R7; SRN6045
LED1, LED2, LED3, LED4: LED3MM
LED1.1, LED1.3, LED2.1, LED3.1, LED4.1: LEDCHIPLED_0603; CHIPLED_0603
LOGO2: OSHW-LOGOL; ESCORNA_LBRESCORNA_CPU_2_10_SPARKFUN-AESTHETICS_OSHW-LOGO-L
R1, R3, R5, R7, R8.1, R9.1, R10.1, R11.1, R13, R21: 1K; R0603
R2, R4: 22R; R0603
R6: 18K; 0204/7
R8, R9, R10, R11: 1K; 0204/7
R12, R14, R15, R16, R17, R19: 10K; 0204/7
R12.1, R14.1, R15.1, R16.1, R17.1, R19.1, R20: 10K; R0603
R13.1: 18K; R0603
R18: 22K; 0204/7
R18.1: 22K; R0603
R22: 3K3; R0603
RED: LEDCHIPLED_0603; CHIPLED_0603
RX: LEDCHIPLED_0603; CHIPLED_0603
S1, S2, S3, S4, S5: 40-XX; B3F-40
S6: B3U-1000P; SMD_157SW
S7: SK12D07; ESCORNA_SK-12D07
SG1: BMT-1205H09; F/CM12P
SJ1: SJ
SV1: MA03-1
U1: CH340ESMD; MSOP10
U3: ASM1117-5.0; SOT223
X1, X1.1: 1776275-2; AK550/2
XH1, XH2, XH3: B5B-XH-A
Y1: CSTCE16M0V53C-R0; RESONATOR

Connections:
5V: C3.2, C7.1, C10.2, C11.2, IC3.4 (VCC), IC3.6 (VCC), IC3.18 (AVCC), ICSP.2, J3.3, J5.4, R7.1, R14.1, R14.1.1, SV1.1, U1.7 (VCC), U3.2 (VOUT), U3.4 (VOUTT)
6V: $1_83_$.P$1, C1.2, C6.2, C6.1.2, C9.2, D4.C, IC2.10 (CD+), R20.1, R22.1, U3.3 (VIN), XH1.P$1, XH2.P$1, XH3.P$1
+D: J2.P3 (D+), R2.2
-D: J2.P2 (D-), R4.2
A0: IC3.23 (PC0(ADC0)), R8.1, R8.1.1
A1: IC3.24 (PC1(ADC1)), R9.1, R9.1.1
A2: IC3.25 (PC2(ADC2)), R10.1, R10.1.1
A3: IC3.26 (PC3(ADC3)), R11.2, R11.1.1
A4: IC3.27 (PC4(ADC4/SDA)), J3.1
A5: IC3.28 (PC5(ADC5/SCL)), J3.2
A6: IC3.19 (ADC6), SV1.2
A7: IC3.22 (ADC7), R14.2, R14.1.2, R19.2, R19.1.2
AREF: C8.1, IC3.20 (AREF)
D0/RX: IC3.30 (PD0(RXD)), J5.2, R3.1
D1/TX: IC3.31 (PD1(TXD)), R5.1, R12.1, R12.1.1
D2: IC2.8 (I8), IC3.32 (PD2(INT0))
D3: IC2.7 (I7), IC3.1 (PD3(INT1))
D4: IC2.6 (I6), IC3.2 (PD4(XCK/T0))
D5: IC2.5 (I5), IC3.9 (PD5(T1))
D6: IC2.4 (I4), IC3.10 (PD6(AIN0))
D7: IC2.3 (I3), IC3.11 (PD7(AIN1))
D8: IC2.2 (I2), IC3.12 (PB0(ICP))
D9: IC2.1 (I1), IC3.13 (PB1(OC1A))
D10: IC3.14 (PB2(SS/OC1B)), JP1.2
D11/MOSI: IC3.15 (PB3(MOSI/OC2)), ICSP.4
D12/MISO: IC3.16 (PB4(MISO)), ICSP.1
D13/SCK: IC3.17 (PB5(SCK)), ICSP.3, R13.1
D+: R2.1, U1.1 (UD+)
D-: R4.1, U1.2 (UD-)
DTR?: C5.2, U1.4 (RTS)
GND: C1.1, C2.1, C3.1, C4.1, C6.1, C6.1.1, C7.2, C8.2, C9.1, C10.1, C11.1, D1.A, D2.A, IC2.9 (GND), IC3.3 (GND), IC3.5 (GND), IC3.21 (AGND), IC4.2 (GND), ICSP.6, J1.2, J2.P5 (GND), J2.S1 (SH1), J2.S2 (SH2), J2.S3 (SH3), J2.S4 (SH4), J2.S5 (SH5), J2.S6 (SH6), J3.4, J5.3, LED1.3.C, R6.2, R13.1.1, R21.2, RED.C, RX.C, S1.3, S1.4 (P1), S2.3, S2.4 (P1), S3.3, S3.4 (P1), S4.3, S4.4 (P1), S5.3, S5.4 (P1), S6.1, SG1.- (2), SJ1.1, SV1.3, U1.3 (GND), U3.1 (GAJ), X1.2, X1.1.2, Y1.2
K: LED1.K (C), LED1.1.C, LED2.K (C), LED2.1.C, LED3.K (C), LED3.1.C, LED4.K (C), LED4.1.C, SJ1.2
ML1: IC2.18 (O1), XH1.P$5, XH3.P$5
ML2: IC2.17 (O2), XH1.P$4, XH3.P$4
ML3: IC2.16 (O3), XH1.P$3, XH3.P$3
ML4: IC2.15 (O4), XH1.P$2, XH3.P$2
MR1: $1_83_$.P$5, IC2.14 (O5), XH2.P$5
MR2: $1_83_$.P$4, IC2.13 (O6), XH2.P$4
MR3: $1_83_$.P$3, IC2.12 (O7), XH2.P$3
MR4: $1_83_$.P$2, IC2.11 (O8), XH2.P$2
unnamed: JP1.1, SG1.+ (1)
unnamed: D1.C, D2.C, F1.2, F1.1.2, S7.P$2 (O)
unnamed: LED2.A, LED2.1.A, R9.2, R9.1.2
unnamed: LED1.A, LED1.1.A, R8.2, R8.1.2
unnamed: LED3.A, LED3.1.A, R10.2, R10.1.2
unnamed: LED4.A, LED4.1.A, R11.1, R11.1.2
unnamed: D3.A, J2.P1 (VBUS)
unnamed: F1.1, F1.1.1, J1.1, X1.1, X1.1.1
unnamed: R1.2, RX.A
unnamed: IC4.3 (FB), R20.2, R21.1
unnamed: IC3.7 (PB6(XTAL1/TOSC1)), Y1.1
unnamed: IC3.8 (PB7(XTAL2/TOSC2)), Y1.3
unnamed: LED1.3.A, R13.2
unnamed: D4.A, IC4.1 (SW), L1.1
unnamed: D3.C, F3.1
unnamed: R22.2, RED.A
unnamed: R5.2, U1.9 (RX)
unnamed: R3.2, U1.8 (TX)
unnamed: R1.1, U1.6 (TNOW)
RAW: C2.2, F3.2, IC4.4 (EN), IC4.5 (VIN), L1.2, S7.P$1, S7.P$3 (S)
RESET: C5.1, IC3.29 (PC6(/RESET)), ICSP.5, R7.2, S6.2
S1: R15.2, R15.1.2, R19.1, R19.1.1, S1.1 (S), S1.2 (S1)
S2: R15.1, R15.1.1, R16.2, R16.1.2, S2.1 (S), S2.2 (S1)
S3: R16.1, R16.1.1, R17.2, R17.1.2, S3.1 (S), S3.2 (S1)
S4: R18.1, R18.1.1, S4.1 (S), S4.2 (S1)
S5: R17.1, R17.1.1, R18.2, R18.1.2, S5.1 (S), S5.2 (S1)
TX3V3: J5.1, R6.1, R12.2, R12.1.2, R13.1.2
U3,3: C4.2, U1.10 (V3)

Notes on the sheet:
Steepers
KEYPAD
BUZZ
CERN Open Hardware Licence -W- V2
Forward
Left
Right
Backward
Choose one Rx.1 = SMD Rx = THT
XDeSIG
PseudoSingularis (PSingularis) by XDeSIG.
0021
Enabling LEDs, Default on
BUZZ on/off
D13
SCL
SDA
ICSP
Bluetooth
RXD
TXD
GND
VCC
RESET
Deseñado en Estrimia con agarimo
SX1308
IC4
USB to ttl serial
Step-up power
MT3608



Board: 2 copper layers, 50.0 x 90.6 mm, 111 parts (9 on the bottom side), 68 nets.

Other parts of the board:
LOGO1: OSHW-LOGOS; OSHW-LOGO-S
U$1: AMTEGA
U$4, U$7, U$8, U$9: FRECHA
U$5: ESCORNABOT; ESCORNA_PEQUE
U$10: GO; VALE
U$12: XDESIG_XDESIG21; XDESIG_XDESIG
XDS, XDS1: XDESIG; XDESIG_CU_2

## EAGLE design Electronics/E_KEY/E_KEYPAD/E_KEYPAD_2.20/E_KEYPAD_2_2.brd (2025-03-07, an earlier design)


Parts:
H1, H2, H3: HOLE3.0; 3,0
LED1, LED2, LED3, LED4: LED3MM
LED1.1, LED2.1, LED3.1, LED4.1: LEDCHIPLED_0603; CHIPLED_0603
LOGO2: OSHW-LOGOS; OSHW-LOGO-S
R1, R2, R3, R4, R7: 10K; 0204/7
R1.1, R2.1, R3.1, R4.1, R7.1: 10K; R0603
R5: 22K; 0204/7
R5.1: 22K; R0603
R6, R8, R9, R10: 1K; 0204/7
R6.1, R8.1, R9.1, R10.1: 1K; R0603
S1, S2, S3, S4, S5: 10-XX; B3F-10XX
S1.1, S2.1, S3.1, S4.1, S5.1: 40-XX; B3F-40XX
SV1: MA04-1
SV2: MA03-1
U$1: ESCORNABOT; ESCORNA_PEQUE
U$3, U$4, U$6, U$11: FRECHA
U$5: GO; VALE
U$7: XDESIG21; XDESIG
U$10: XDESIG; XDESIG_CU_2

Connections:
5V: R7.1, R7.1.1, SV2.1
A0: R6.1, R6.1.1, SV1.1
A1: R8.1, R8.1.1, SV1.2
A2: R9.1, R9.1.1, SV1.3
A3: R10.2, R10.1.1, SV1.4
GND: LED1.K (C), LED1.1.C, LED2.K (C), LED2.1.C, LED3.K (C), LED3.1.C, LED4.K (C), LED4.1.C, S1.1 (S), S1.2 (S1), S1.1.1 (S), S1.1.2 (S1), S2.1 (S), S2.2 (S1), S2.1.1 (S), S2.1.2 (S1), S3.1 (S), S3.2 (S1), S3.1.1 (S), S3.1.2 (S1), S4.1 (S), S4.2 (S1), S4.1.1 (S), S4.1.2 (S1), S5.1 (S), S5.2 (S1), S5.1.1 (S), S5.1.2 (S1), SV2.3
unnamed: LED2.A, LED2.1.A, R8.2, R8.1.2
unnamed: LED1.A, LED1.1.A, R6.2, R6.1.2
unnamed: LED3.A, LED3.1.A, R9.2, R9.1.2
unnamed: LED4.A, LED4.1.A, R10.1, R10.1.2
S1: R1.1, R1.1.1, R2.2, R2.1.2, S1.3, S1.4 (P1), S1.1.3, S1.1.4 (P1)
S2: R2.1, R2.1.1, R3.2, R3.1.2, S2.3, S2.4 (P1), S2.1.3, S2.1.4 (P1)
S3: R3.1, R3.1.1, R4.2, R4.1.2, S3.3, S3.4 (P1), S3.1.3, S3.1.4 (P1)
S4: R5.1, R5.1.1, S4.3, S4.4 (P1), S4.1.3, S4.1.4 (P1)
S5: R4.1, R4.1.1, R5.2, R5.1.2, S5.3, S5.4 (P1), S5.1.3, S5.1.4 (P1)
SIG: R1.2, R1.1.2, R7.2, R7.1.2, SV2.2

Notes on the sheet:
For Pull-up into the cpu, not place R7 (R7.1)
001
Creative commons. Attribution-ShareAlike 4.0 International (CC BY-SA 4.0) By XDeSIG
XDeSIG
KEYPAD
Choose one Rx.1 = SMD Rx = THT
SX.1 SW12mm
SX SW 6mm
Forward
Left
Right
Backward
D13
Designed in Kalekói



Board: 2 copper layers, 48.4 x 46.4 mm, 56 parts (4 on the bottom side), 16 nets.

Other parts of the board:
LOGO1: OSHW-LOGOS; OSHW-LOGO-S
U$2: ESCORNABOT; ESCORNA_PEQUE
U$8: XDESIG; XDESIG_CU_2
U$9: XDESIG21; XDESIG

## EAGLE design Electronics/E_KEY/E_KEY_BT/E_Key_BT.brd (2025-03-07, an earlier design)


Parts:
C5, C8: 10uF/16V; C1206
CN1: JST_2PIN-THM-RA; JST-PH-2-THM-RA
F1: Fus 0.5A; R1206
J1, J2, J3, J4, J5, J6, J9: Hole; BANANA_CONN
LED1: LED3MM
MD1: PRO_MICRO
R1, R2, R3, R4, R5, R6: 22M; R0603
R7: 1K; R0603
R20: 10K; R0603
R21: 18K; R0603
SV1: FE08-1; FE08
U1: DD05CVSA
U3: BLUETOOTH; BLUETOOTH_MODULE
U4: 1117ST3.3; SOT223
U$1: USB_PCB
U$2: ESCORNA_SK12F14D; ESCORNA_SK-12D07

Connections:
3V3: C8.1, SV1.8, U4.4 (OUT)
+5V: MD1.21 (VCC), R1.2, R2.2, R3.2, R4.2, R5.2, R6.2, U3.5 (+5V)
GND: C5.2, C8.2, CN1.2 (1), J9.P$1, LED1.K (C), MD1.3 (GND1), MD1.4 (GND), MD1.23 (GND2), R21.1, SV1.6, U1.P$2 (GND), U1.P$4 (GNDB), U1.P$5 (GNDO), U3.4 (GND), U4.1 (GND/ADJ), U$1.1 (GND)
LED: MD1.17 (A0), R7.2
MISO: MD1.15 (14), SV1.4
MK1: J1.P$1, MD1.7 (4), R1.1
MK2: J2.P$1, MD1.9 (6), R2.1
MK3: J3.P$1, MD1.11 (8), R3.1
MK4: J4.P$1, MD1.18 (A1), R4.1
MK5: J5.P$1, MD1.19 (A2), R5.1
MK6: J6.P$1, MD1.20 (A3), R6.1
MOSI: MD1.14 (16), SV1.3
unnamed: U1.P$6 (VOUT), U$2.P$2 (O)
unnamed: LED1.A, R7.1
unnamed: F1.1, U1.P$1 (VIN)
unnamed: CN1.1 (2), U1.P$3 (BAT)
RST: MD1.13 (10), SV1.7
RX1: MD1.2 (RX1), U3.3 (TX)
SCK: MD1.16 (15), SV1.2
SDA: MD1.5 (2), SV1.1
TX1: MD1.1 (TX1), R20.1
TX3V3: R20.2, R21.2, U3.2 (RX)
UVCC: F1.2, U$1.5 (VBUS)
VRAW: C5.1, MD1.24 (RAW), U4.3 (IN), U$2.P$1, U$2.P$3 (S)

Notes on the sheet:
001



Board: 2 copper layers, 50.5 x 50.8 mm, 31 parts (16 on the bottom side), 24 nets.

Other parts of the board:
U$3: XDESIG_CU
U$4: BODY
U$5: XDESIG

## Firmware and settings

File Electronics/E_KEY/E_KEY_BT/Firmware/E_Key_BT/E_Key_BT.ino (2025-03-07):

/*
    Teclado para Escornabot con sensores tipo MakeyMakey na placa E_KEY_BT
    pódese por calquera obxecto que conduza minimamente a corrente,
    axustando o valor umbral: maior para menos sensibilidade
    *
    Necesitamos 2 módulos Bluetooth, un Mestre e outro Escravo. 
    un HC-05 como Mestre e outro escravo que pode ser HC-05 ou HC-06
    
HC-05 como Mestre. 
    Conectaremos o modulo mediante un adaptador USB - RS-232 TTL. Axustes do terminal Baud 38400 ,NL & CR. 
   
    Comandos AT HC-05 (Pulsar reset durante o acendido, (Parpadeo lento)):
    
                Envío               -  Resposta
    test:       AT                  -  OK
    nome:       AT+NAME=<NOME>      -  OK ( preguntar é AT+NAME?, resposta o nome )
    pin         AT+PSWD="<pin>"     -  OK ( AT+PSWD="1234" o mesmo que no escravo)
    Velocidade  AT+UART=9600,0,0    -  OK ( a mesma velocidade que no escravo )
    rol:        AT+ROLE=<rol>       -  OK ( 0=escravo, 1=Mestre (precisa reinicio (pulsar reset mentras se inicia )))
    modo:       AT+CMODE=<mode>     -  OK ( 0=conexión a un enderezo especifico(Bind), 1=conectase o primeiro dispositivo que atopa e se queda ligado a el )
    amarre:     AT+BIND=<enderezo>  -  OK ( Enderezo do escravo no seguinte formato  AT+BIND=98D3,31,7028EF )
    RESET       AT+RESET            -  OK ( Reinicia gardando os datos)
    +info: https://goo.gl/YTYMmm
HC-06 escravo. 
     Conectaremos o modulo mediante un adaptador USB - RS-232 TTL. Axustes do terminal Baud 9600, sen axuste de liña ou NL & CR, NESTE CASO RESPONDE OS COMANDOS DOS HC05.
                Envío             -  Resposta
    test:       AT                -  OK
    nome:       AT+NAME<NOME>     -  OKsetname
    pin         AT+PIN<pin>       -  OKsetPIN ( AT+PIN1234 o mesmo pin que no mestre )
    Velocidade  AT+BAUD4          -  OK9600 ( 4 = 9600 baud ( a mesma velocidade que no mestre ))
    
    XDeSIG 2018 Creative Commons BY-SA4.0.
*/

// A2 Entrada tecla leste (e)
// A7 Entrada tecla oeste (o)
// A6 Entrada tecla norte (n)
// A8 Entrada tecla sur (n)

// A3 Entrada tecla executa (g)

#define led 11 //led para indicar o funcionamento

int entradas [5] = {A0, A2, A3, A4, A5};      //os pines de entrada
char teclas [5] = {'e','n','w','s','g'};  //cadea a enviar vía serie o escornabot


int umbral = 1000;   //Valor a partires do cal se detecta pulsacion ( sensibilidade)
int valor = 0;      //Variable para al macenar o valor da lectura analoxica

int contador = 0;   //Variable do contador

void setup() {
  
  Serial.begin(9600);   //activación da canle serie a 9600bps
  Serial1.begin(9600);   //activación da canle serie 1 a 9600bps

  
 // configuración dos pines de entrada
  for (contador = 0 ; contador < 6; contador ++) {
    pinMode(entradas[contador], INPUT);
  }

// configuración dos pines de saida ( leds)
    pinMode(led, OUTPUT);
  }
 
 
  void loop() {

    for (contador = 0 ; contador < 5; contador ++) {
      
      valor = analogRead(entradas[contador]);     //Collemos valor da entrada correspondente
      
      if (valor > umbral) {                       //Comprobamos se o valor supera o umbral de sensibilidade
        
        Serial1.print (teclas [contador]);         //Enviamos o comando da tecla seguido do retorno de carro
         Serial1.print ("\n");
        
        Serial.print ("Enviando: ");
          Serial.println (teclas [contador]);
        
        Serial.print ("Lectura: ");
          Serial.println (valor);
        
        digitalWrite (led, HIGH);
        delay(200);
        digitalWrite (led, LOW);
        delay(500);
      }
      delay(1); //Retardo entre lecturas
    }

  }

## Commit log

2019-05-26 Update E_KEY_BT
    [Base_E_Key_BT.stl, E_Key_BT.brd, E_Key_BT.sch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]
2019-10-01 Update BOM
    [Escorna_CPU_2_20_BOM.ods]
2019-10-17 Add DXF, and rename
    [E_KEYPAD_2_2.brd, E_KEYPAD_2_2.sch, E_KEYPAD_2_2_top.dxf]
2020-05-25 Up CPU_2.40
    [Escorna_CPU_2_40.brd, Escorna_CPU_2_40.sch]
2020-09-24 Update Amtega version
    [Escorna_CPU_2_40Amt.brd, Escorna_CPU_2_40Amt.sch]
2021-06-04 Update rev002
    [Escorna_CPU_2_40Amt.brd, Escorna_CPU_2_40Amt.sch, Tapa_2_40.FCStd]
2023-03-12 Update links
    [Escorna_CPU_2_12_BOM.ods]
2023-03-19 Update Bomm
    [Escorna_CPU_1_20_BOM.xlsx]
2025-03-07 User update
    User update
    [Base_E_Key_BT.stl, BotMotShielArdu.brd, BotMotShielArdu.sch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]

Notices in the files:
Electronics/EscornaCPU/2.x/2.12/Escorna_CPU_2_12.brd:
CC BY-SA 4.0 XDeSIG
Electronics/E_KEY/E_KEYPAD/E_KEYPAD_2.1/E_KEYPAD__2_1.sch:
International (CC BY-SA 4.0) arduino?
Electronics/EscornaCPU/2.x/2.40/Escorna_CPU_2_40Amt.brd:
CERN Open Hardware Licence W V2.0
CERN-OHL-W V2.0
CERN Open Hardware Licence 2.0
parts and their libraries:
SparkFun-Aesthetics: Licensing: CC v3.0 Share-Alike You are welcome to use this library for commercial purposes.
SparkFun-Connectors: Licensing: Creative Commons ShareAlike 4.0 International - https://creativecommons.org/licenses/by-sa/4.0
